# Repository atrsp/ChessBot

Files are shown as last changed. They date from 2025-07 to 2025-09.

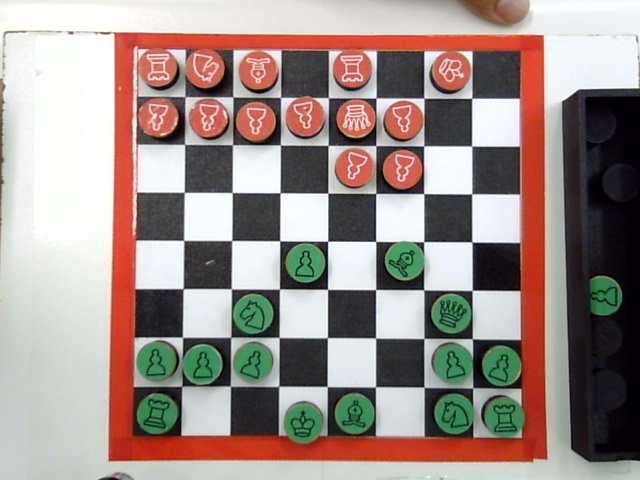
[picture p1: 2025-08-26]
server/vision/before.jpg

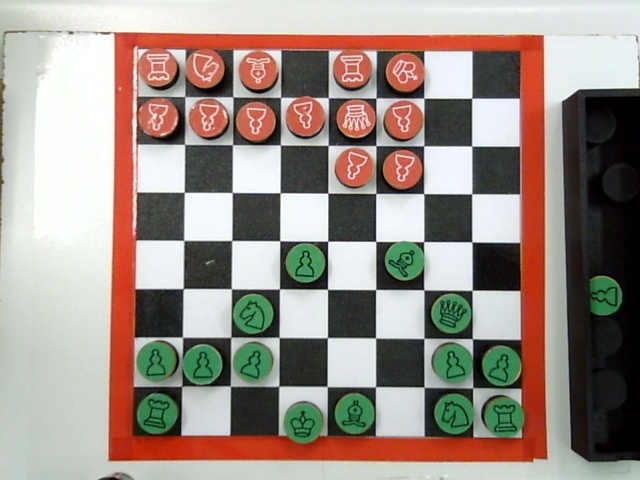
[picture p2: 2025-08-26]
server/vision/after.jpg

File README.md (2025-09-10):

# ChessBOT

## Visão Geral

O ChessBOT é um projeto de um jogador de xadrez autônomo, materializado em uma garra robótica capaz de disputar uma partida de xadrez contra um oponente humano de forma independente. O sistema utiliza visão computacional para identificar as jogadas do adversário, uma engine de xadrez para calcular seus próprios movimentos e um braço robótico para mover as peças no tabuleiro.

Este projeto foi desenvolvido como parte da disciplina [PROJETO INTEGRADO DE COMPUTAÇÃO II](https://computacao-ufes.github.io/mostra/pic2_EC_20251.html) na Universidade Federal do Espírito Santo (UFES).



### Autores
* [Ana Tereza Ribeiro Soares Pereira](https://github.com/atrsp)
* [Felipe Mattos Vanetti de Albuquerque](https://github.com/felipemattosv)
* [Luiz Felipe Machado](https://github.com/luizfelmach)
* [Vitor Dadalto Câmara Gomes](https://github.com/vitordcgomes)

---

## Componentes e Materiais

A seguir estão os itens utilizados na construção do ChessBOT.

### Componentes Eletrônicos e Estruturais
* **Microcontrolador:** ESP32
* **Servomotores:** 3 unidades do modelo Tower Pro MG995
* **Eletroímã:** 1 unidade com capacidade de 2kg
* **Webcam:** Logitech C720
* **Botões:** 2 Botões de Fliperama
* **Estrutura de Madeira:**
    * 1 Tábua de 45cm x 35cm
    * 1 "Ponte" de madeira com 55cm de altura

### Impressão 3D e Materiais Adicionais
* **Impressora 3D**
* **Filamento:** PLA
* **Peças:** 32 moedas de R$0,10
* **Acabamento:**
    * Papel Contact
    * Adesivos de papel para as peças

---

## Hardware e Impressão 3D

A estrutura física do braço robótico e suas peças foram produzidas com uma impressora 3D.

### Braço Robótico
O modelo base utilizado para o braço foi o [EEZYbotARM MK2](https://www.thingiverse.com/thing:1454048), um projeto gratuito desenvolvido por "daGHIZmo".

### Modificações e Melhorias
O modelo original serviu como ponto de partida, mas não possuía o alcance e a precisão necessários para a aplicação. Por isso, foi necessário remodelar algumas peças.

* **Engrenagem:** Após a montagem, foi identificada uma grande folga na engrenagem, causando uma imprecisão de uma casa no tabuleiro. A peça foi redesenhada para corrigir seu módulo, o que diminuiu a folga.
* **Base do Eletroímã:** O projeto original possuía uma garra na ponta do braço. Como o ChessBOT utiliza um eletroímã, foi modelada uma nova peça para acoplar este componente.

### Peças de Xadrez
Foram desenvolvidas e impressas bases para as moedas para facilitar o movimento do braço ao pegar cada peça e aumentar a jogabilidade do oponente.

### Peças Auxiliares
Também foram impressos modelos 3D para componentes de suporte, como dois suportes para descarte de peças capturadas e dois suportes para os botões.

---

## Montagem

A montagem do braço robótico seguiu as instruções detalhadas no vídeo [EEZYbotARM MK2 3D Printed Robot Build - Chris's Basement](https://www.youtube.com/watch?v=R2MI-tpXyS4&ab_channel=ChrisRiley) de Chris Riley. Não foi feita nenhuma alteração nesse processo.

---

## Software

O software do ChessBOT é dividido em dois componentes principais: o sistema de visão computacional para detectar a jogada do oponente e a engine de xadrez para a tomada de decisão.

### Visão Computacional
Foi utilizada a biblioteca [**OpenCV**](https://opencv.org/) em Python para identificar a jogada do oponente. A estratégia consiste em capturar uma imagem do tabuleiro antes e outra depois do movimento do oponente para identificar as diferenças.

O processo ocorre em três etapas:

1.  **Identificação do Tabuleiro:** Uma máscara de cor vermelha é aplicada à imagem para destacar a borda do tabuleiro. Com isso, os pontos referentes às bordas são detectados para saber onde cortar a imagem.
2.  **Corte e Ajuste de Perspectiva:** A imagem passa por uma transformação de perspectiva (warp) para corrigir distorções causadas pelo ângulo da câmera, alinhando o tabuleiro em uma visão superior. Em seguida, a área é cortada, deixando apenas a região útil.
3.  **Detecção do Movimento:** Com as imagens "antes" e "depois" normalizadas, o sistema calcula a diferença entre elas. Uma operação com kernel é aplicada para reduzir ruídos. As diferenças mais significativas são usadas para determinar o movimento realizado.

### Engine de Xadrez
A inteligência do robô é fornecida pela [**Stockfish**](https://stockfishchess.org/), uma engine de xadrez de código aberto.

* **Funcionamento:** A Stockfish recebe a configuração atual do tabuleiro (a disposição das peças no tabuleiro) e calcula qual seria a melhor jogada.
* **Análise:** Além de sugerir a jogada, a engine fornece uma avaliação numérica que indica se as peças brancas ou pretas estão em vantagem e o tamanho dessa vantagem.

---

## Decisões de Projeto

Algumas decisões foram tomadas para garantir a funcionalidade e a robustez do sistema.

* **Botões de Confirmação:** Foram adicionados botões de confirmação de jogada para determinar o momento exato de tirar a foto que identificará o movimento do oponente.
* **Adesivos das Peças:** As cores vermelha e verde foram escolhidas por se diferenciarem bem do preto e branco do tabuleiro, facilitando a identificação da jogada por visão computacional.
---

## Organização do repositório

Neste repositório, além do código principal, que integra a visão computacional com a lógica de jogo e a engine de xadrez, também existe uma interface que facilita o mapeamento das posições do tabuleiro.

## Como rodar?

### Pré-requisitos

Antes de iniciar, garanta que você possui configurado em sua máquina:  
- Visual Studio Code ([VSCode](https://code.visualstudio.com/))
- Extensão [PlatformIO](https://platformio.org/install/ide?install=vscode) no VSCode  
- [Node.js v20.19.4](https://nodejs.org/en/download/)  
- [Python 3.13.5](https://www.python.org/downloads/)  
- [Mosquitto MQTT Broker](https://mosquitto.org/download/)  
- Webcam conectada ao computador  
- Sistema operacional Linux (ou adaptado para Windows/macOS, quando aplicável)
- O ESP32 e a máquina que estará responsável pelos servidores durante o jogo devem sempre estar conectados na mesma rede WiFi.
  - Para verificar o IP da sua máquina na rede, utilize `ifconfig`.

---

### Passo a Passo para rodar a interface de mapeamento (apenas durante a etapa de mapeamento das posições do tabuleiro).
     
1. Configure o **Mosquitto Broker**.  
   Edite o arquivo `/etc/mosquitto/mosquitto.conf` com o seguinte conteúdo:  
   ```conf
   listener 1883
   protocol mqtt

   listener 9001
   protocol websockets

   allow_anonymous true
   ```  
   Inicie o serviço:  
   ```bash
   sudo systemctl start mosquitto.service
   ```
   
2. Configuração do Hardware (ESP32):
   - Abra o **VSCode** com a extensão **PlatformIO**.  
   - Abra a pasta `Hardware/`.  
      - As dependências serão instaladas automaticamente via `platformio.ini`.
   - Configure as constantes no arquivo `Hardware/map.cpp` (nome e senha da rede Wi-Fi, IP do broker e tópico MQTT).
   - Compile e envie o código `map.cpp` para o ESP32 com o PlatformIO. Tenha em mente que somente o código que está dentro da pasta `src/` é compilado e enviado para o microcontrolador.

3. Acesse a interface de mapeamento:  
   - Entre na pasta `ui/`.  
   - Instale as dependências:  
     ```bash
     npm install
     ```  
   - Rode o servidor:  
     ```bash
     npm run dev
     ```  
   - Acesse em: [`http://localhost:3000`](http://localhost:3000).  

4. Salve os valores dos servos para cada posição do tabuleiro em `hardware/lib/board/board.hpp`
---

### Passo a Passo para rodar o Servidor de Inteligência (Engine + Visão Computacional).

1. Baixe o **Stockfish** em: [https://stockfishchess.org/download/](https://stockfishchess.org/download/).  
2. Mova o binário para:  
   ```bash
   /usr/local/bin/stockfish
   ```
   Ou altere a constante `STOCKFISH_PATH` no arquivo `server/src/main.py` com o caminho para o local da sua instalação da stockfish.

3. Vá para a pasta `server/` e crie um ambiente virtual:  
   ```bash
   python3 -m venv .venv
   source .venv/bin/activate
   ```  

4. Instale as dependências:  
   ```bash
   pip install -r requirements.txt
   ```  

5. Certifique-se de que a webcam está funcionando.  

6. Inicie o servidor Python:  
   ```bash
   python3 src/main.py
   ```  

---

### Configuração da Interface do Jogo
1. Configuração do Hardware (ESP32):
   - Abra o **VSCode** com a extensão **PlatformIO**.  
   - Abra a pasta `Hardware/`.  
      - As dependências serão instaladas automaticamente via `platformio.ini`.
   - Configure as constantes no arquivo `Hardware/main.cpp` (IP do servidor e porta do servidor criado na etapa anterior (Servidor de Inteligência)).
      - O nome e senha da rede WiFi também precisam ser alterados dentro da função `void setup()`
   - Compile e envie o código `main.cpp` para o ESP32 com o PlatformIO. Tenha em mente que somente o código que está dentro da pasta `src/` é compilado e enviado para o microcontrolador.
     
2. Entre na pasta `chess/`.  
3. Instale as dependências:  
   ```bash
   npm install
   ```  
4. Rode o servidor da interface:  
   ```bash
   npm run dev
   ```
5. Acesse o servidor em: [`http://localhost:3000`](http://localhost:3000).
6. Se precisar reiniciar o jogo, basta clicar no botão de reset no ESP32 e reorganizar as peças no tabuleiro.

---

## Fluxo Geral de Execução (Mapeamento das posições do tabuleiro):
1. Iniciar o **Broker MQTT (Mosquitto)** com o comando
   ```bash
   sudo systemctl start mosquitto.service
   ```
2. Alterar as constantes da rede WiFi e Broker no arquivo `hardware/map.cpp` e subir o código no **ESP32** pelo PlatformIO.  
3. Abrir a **Interface de Mapeamento** na pasta `ui/` com `npm run dev` em [`http://localhost:3000`](http://localhost:3000) para calibrar as posições do tabuleiro.
4. Salvar as posições mapeadas em `hardware/lib/board/board.hpp`.

## Fluxo Geral de Execução (Jogo completo):
1. Dentro da pasta `server/`, ative o **ambiente virtual (.venv)** rodando o seguinte comando.
   ```bash
   source .venv/bin/activate
   ```
2. Iniciar o **servidor Python** com Stockfish + visão computacional em `server/src/main.py`
3. Alterar as constantes da rede WiFi e IP do server python no arquivo `hardware/src/main.cpp` e subir o código no **ESP32** pelo PlatformIO.  
4. Abrir a **Interface do Jogo** na pasta `chess/` com `npm run dev` em [`http://localhost:3000`](http://localhost:3000) para começar a jogar contra o braço robótico.  

### Opcional:
A parte de visão computacional (identificação de movimentação das peças) pode ser testada separadamente via Jupyter Notebook na pasta `server/vision/`:

   - O arquivo `takepic.py` é útil para descomplicar o processo de tirar uma foto antes e depois de mudar uma peça de uma posição para outra no tabuleiro e pode ser rodado primeiro para armazenar as fotos `before.jpg` e `after.jpg`   
   - O Notebook `main.ipynb` carrega as imagens `before.jpg` e `after.jpg` e mostra todo o processamento sobre as imagens para identificar em quais posições do tabuleiro houve mudança. É útil para debuggar possíveis erros de identificação da jogada do oponente que possam ocorrer durante o jogo.

***
***

# ChessBOT (English)

## Overview

ChessBOT is an autonomous chess player project, embodied by a robotic arm capable of playing a game of chess against a human opponent on its own. The system uses computer vision to identify the opponent's moves, a chess engine to calculate its own moves, and a robotic arm to move the pieces on the board.

This project was developed as part of the "INTEGRATED COMPUTING PROJECT II" course at the Federal University of Espírito Santo.

### Authors
* [Ana Tereza Ribeiro Soares Pereira](https://github.com/atrsp)
* [Felipe Mattos Vanetti de Albuquerque](https://github.com/felipemattosv)
* [Luiz Felipe Machado](https://github.com/luizfelmach)
* [Vitor Dadalto Câmara Gomes](https://github.com/vitordcgomes)

---

## Components and Materials

The following are the items used in the construction of the ChessBOT.

### Electronic and Structural Components
* **Microcontroller:** ESP32
* **Servo Motors:** 3 units of the Tower Pro MG995 model
* **Electromagnet:** 1 unit with a 2kg capacity
* **Webcam:** Logitech C720
* **Buttons:** 2 Arcade Buttons
* **Wooden Structure:**
    * 1 45cm x 35cm wooden board
    * 1 wooden "bridge" with a height of 55cm

### 3D Printing and Additional Materials
* **3D Printer**
* **Filament:** PLA
* **Pieces:** 32 Brazilian 10-cent coins
* **Finishing:**
    * Contact Paper
    * Paper stickers for the pieces

---

## Hardware and 3D Printing

The physical structure of the robotic arm and its parts were produced using a 3D printer.

### Robotic Arm
The base model used for the arm was the [EEZYbotARM MK2](https://www.thingiverse.com/thing:1454048), a free design developed by "daGHIZmo".

### Modificações and Improvements
The original model served as a starting point, but it lacked the necessary reach and precision for the application. Therefore, it was necessary to remodel some parts.

* **Gear:** After assembly, a large backlash was identified in the gear, causing an imprecision of one square on the board. The part was redesigned to correct its module, which reduced the backlash.
* **Electromagnet Base:** The original design featured a claw at the end of the arm. As the ChessBOT uses an electromagnet, a new part was modeled to attach this component.

###Chess Pieces
Bases for the coins were developed and printed to make it easier for the arm to pick up each piece and to improve the opponent's gameplay experience.

### Auxiliary Parts
3D models were also printed for support components, such as two holders for captured pieces and two holders for the buttons.

---

## Assembly

The assembly of the robotic arm followed the detailed instructions in the video [EEZYbotARM MK2 3D Printed Robot Build - Chris's Basement](https://www.youtube.com/watch?v=R2MI-tpXyS4&ab_channel=ChrisRiley) by Chris Riley. No alterations were made to this process.

---

## Software

The ChessBOT's software is divided into two main components: the computer vision system to detect the opponent's move and the chess engine for decision-making.

### Computer Vision
The [**OpenCV**](https://opencv.org/) library in Python was used to identify the opponent's move. The strategy is to capture an image of the board before and another after the opponent's move to identify the differences.

The process occurs in three stages:

1.  **Board Identification:** A red color mask is applied to the image to highlight the board's border. This allows the detection of the points corresponding to the borders to know where to crop the image.
2.  **Cropping and Perspective Adjustment:** The image undergoes a perspective transformation (warp) to correct distortions caused by the camera angle, aligning the board to a top-down view. Then, the area is cropped, leaving only the useful region.
3.  **Move Detection:** With the normalized "before" and "after" images, the system calculates the difference between them. A kernel operation is applied to reduce noise. The most significant differences are used to determine the move that was made.

### Chess Engine
The robot's intelligence is provided by [**Stockfish**](https://stockfishchess.org/), an open-source chess engine.

* **Functionality:** Stockfish receives the current board configuration (the "position") and calculates what the best move would be.
* **Analysis:** In addition to suggesting a move, the engine provides a numerical evaluation that indicates whether the white or black pieces have an advantage and the size of that advantage.

---

## Design Decisions

Certain decisions were made to ensure the system's functionality and robustness.

* **Confirmation Buttons:** Move confirmation buttons were added to determine the exact moment to take the photo that will identify the opponent's move.
* **Piece Stickers:** The red and green colors were chosen because they differentiate well from the black and white of the board, facilitating the move identification by computer vision.

## How to run?

### Prerequisites

Before you start, make sure your machine has:

* Visual Studio Code ([VSCode](https://code.visualstudio.com/))
* [PlatformIO extension](https://platformio.org/install/ide?install=vscode) in VSCode
* [Node.js v20.19.4](https://nodejs.org/en/download/)
* [Python 3.13.5](https://www.python.org/downloads/)
* [Mosquitto MQTT Broker](https://mosquitto.org/download/)
* A webcam connected to the computer
* Linux operating system (or adapted for Windows/macOS where applicable)
* The ESP32 and the machine responsible for running the servers during the game must always be connected to the same Wi-Fi network.

  * To check your machine’s IP on the network, use `ifconfig`.

---

### Step-by-step to run the mapping interface (only during the board-position mapping stage).

1. Configure the **Mosquitto Broker**.
   Edit `/etc/mosquitto/mosquitto.conf` with the following content:

   ```conf
   listener 1883
   protocol mqtt

   listener 9001
   protocol websockets

   allow_anonymous true
   ```

   Start the service:

   ```bash
   sudo systemctl start mosquitto.service
   ```

2. Hardware Setup (ESP32):

   * Open **VSCode** with the **PlatformIO** extension.
   * Open the `Hardware/` folder.

     * Dependencies will be installed automatically via `platformio.ini`.
   * Set the constants in `Hardware/map.cpp` (Wi-Fi SSID and password, broker IP, and MQTT topic).
   * Compile and upload `map.cpp` to the ESP32 with PlatformIO. Keep in mind that only the code inside the `src/` folder is compiled and uploaded to the microcontroller.

3. Access the mapping interface:

   * Go into the `ui/` folder.
   * Install dependencies:

     ```bash
     npm install
     ```
   * Run the dev server:

     ```bash
     npm run dev
     ```
   * Open: [`http://localhost:3000`](http://localhost:3000).

4. Save the servo values for each board position in `hardware/lib/board/board.hpp`

---

### Step-by-step to run the Intelligence Server (Engine + Computer Vision).

1. Download **Stockfish** at: [https://stockfishchess.org/download/](https://stockfishchess.org/download/).

2. Move the binary to:

   ```bash
   /usr/local/bin/stockfish
   ```

   Or change the `STOCKFISH_PATH` constant in `server/src/main.py` to the path where Stockfish is installed on your system.

3. Go to the `server/` folder and create a virtual environment:

   ```bash
   python3 -m venv .venv
   source .venv/bin/activate
   ```

4. Install dependencies:

   ```bash
   pip install -r requirements.txt
   ```

5. Make sure the webcam is working.

6. Start the Python server:

   ```bash
   python3 src/main.py
   ```

---

### Game Interface Setup

1. Hardware Setup (ESP32):

   * Open **VSCode** with the **PlatformIO** extension.
   * Open the `Hardware/` folder.

     * Dependencies will be installed automatically via `platformio.ini`.
   * Set the constants in `Hardware/main.cpp` (server IP and the port of the server created in the previous step—Intelligence Server).

     * The Wi-Fi SSID and password also need to be set inside the `void setup()` function.
   * Compile and upload `main.cpp` to the ESP32 with PlatformIO. Keep in mind that only the code inside the `src/` folder is compiled and uploaded to the microcontroller.
2. Go into the `chess/` folder.
3. Install dependencies:

   ```bash
   npm install
   ```
4. Run the interface server:

   ```bash
   npm run dev
   ```
5. Access the interface at: [`http://localhost:3000`](http://localhost:3000).
6. If you need to restart the game, just press the reset button on the ESP32 and rearrange the pieces on the board.

---

## Overall Execution Flow (Board position mapping):

1. Start the **MQTT Broker (Mosquitto)** with:

   ```bash
   sudo systemctl start mosquitto.service
   ```
2. Update the Wi-Fi and Broker constants in `hardware/map.cpp` and upload the code to the **ESP32** via PlatformIO.
3. Open the **Mapping Interface** in the `ui/` folder with `npm run dev` at [`http://localhost:3000`](http://localhost:3000) to calibrate the board positions.
4. Save the mapped positions in `hardware/lib/board/board.hpp`.

## Overall Execution Flow (Full game):

1. Inside the `server/` folder, activate the **virtual environment (.venv)** by running:

   ```bash
   source .venv/bin/activate
   ```
2. Start the **Python server** with Stockfish + computer vision at `server/src/main.py`.
3. Update the Wi-Fi constants and the Python server IP in `hardware/src/main.cpp` and upload the code to the **ESP32** via PlatformIO.
4. Open the **Game Interface** in the `chess/` folder with `npm run dev` at [`http://localhost:3000`](http://localhost:3000) to start playing against the robotic arm.

### Optional:

The computer vision component (identifying piece movement) can be tested separately via Jupyter Notebook in the `server/vision/` folder:

* The `takepic.py` file is useful to simplify taking a photo before and after moving a piece from one square to another, and can be run first to store the `before.jpg` and `after.jpg` images.
* The `main.ipynb` notebook loads `before.jpg` and `after.jpg` and shows the entire processing pipeline on the images to identify which board squares changed. It’s useful for debugging possible errors in detecting the opponent’s move that may occur during the game.

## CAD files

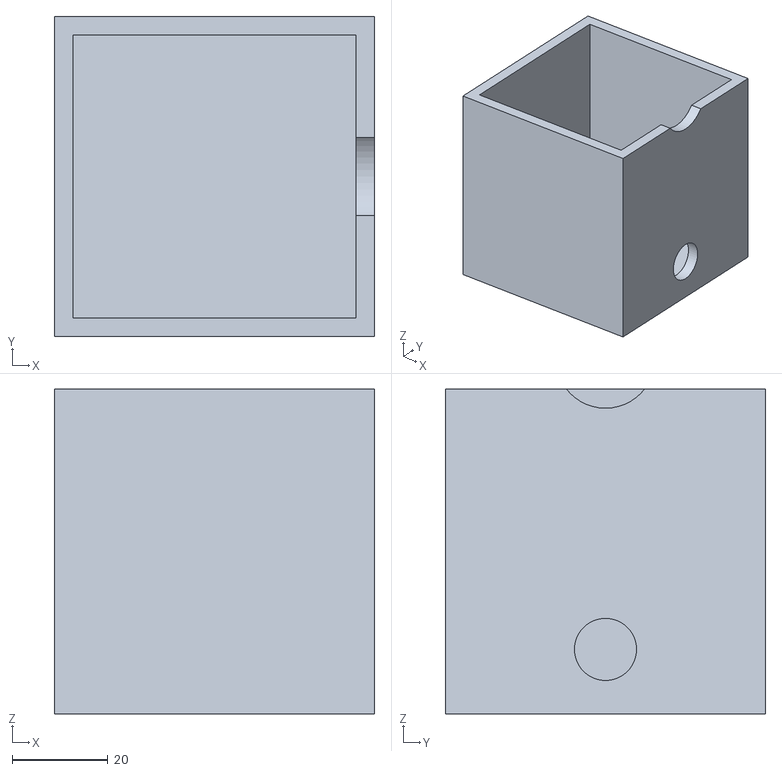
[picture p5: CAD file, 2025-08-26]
3D/buttonBox/corpo_caixa (1).stl
67.0 x 67.0 x 68.0

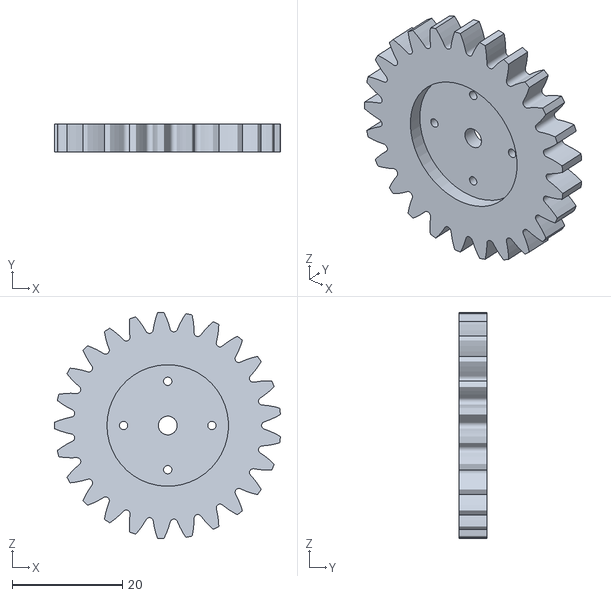
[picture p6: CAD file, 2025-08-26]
3D/EEZYbotARMMk2_changes/Engrenagem_pequena_nova.stl
40.9 x 5.00 x 41.0

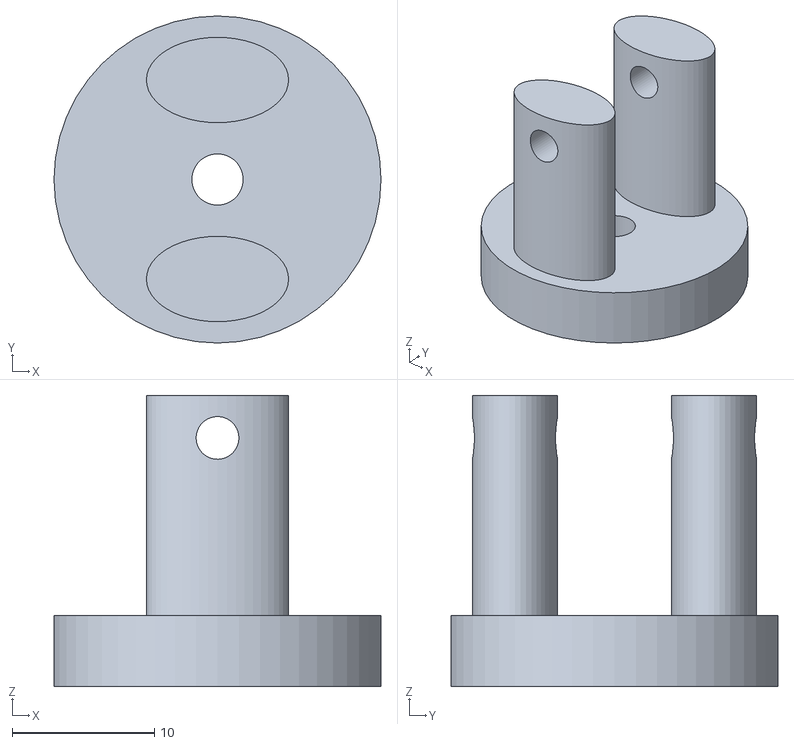
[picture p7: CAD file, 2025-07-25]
3D/electromagnetBase/encaixe_eletroima.stl
23.0 x 23.0 x 20.5

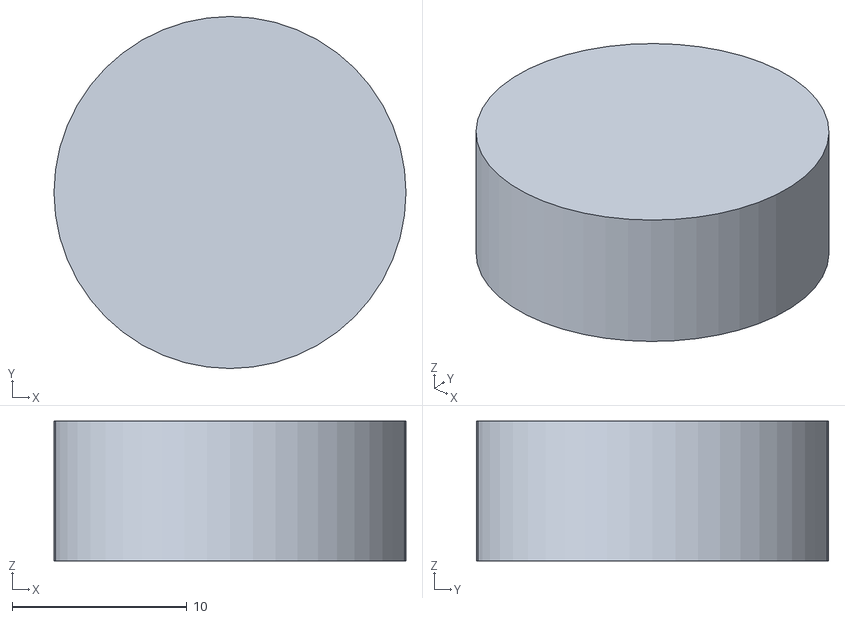
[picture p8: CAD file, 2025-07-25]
3D/pieceBase/semParede.stl
20.1 x 20.2 x 8.00

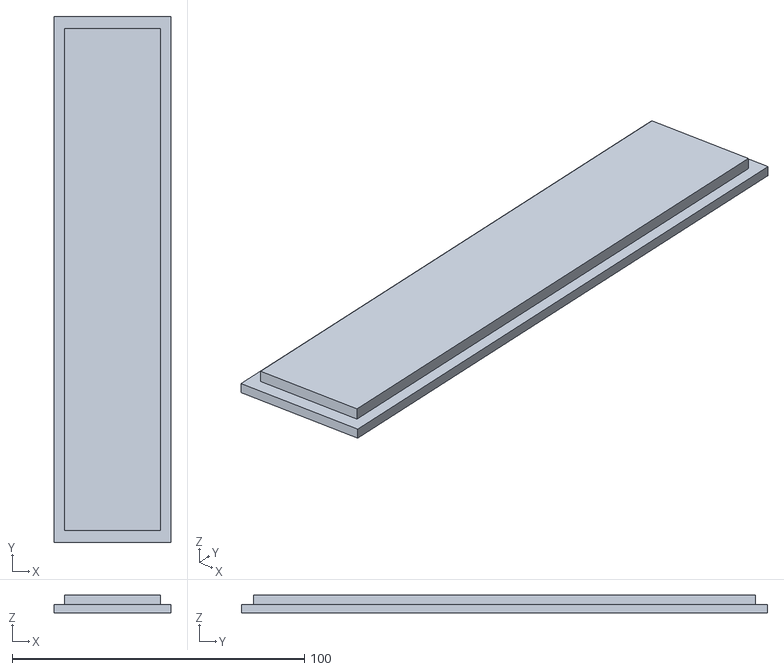
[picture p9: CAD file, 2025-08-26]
3D/pieceTrash/tampa_lixo (1).stl
40.0 x 180.0 x 6.00

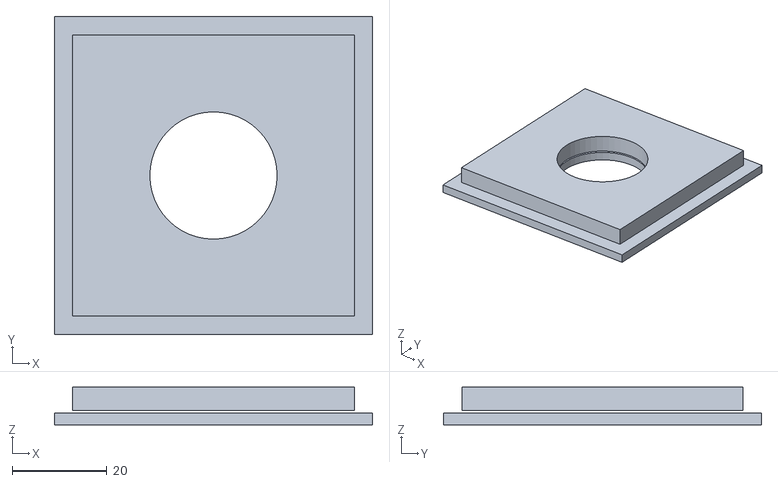
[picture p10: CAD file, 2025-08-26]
3D/buttonBox/tampa_caixa (1).stl
67.0 x 67.0 x 8.00

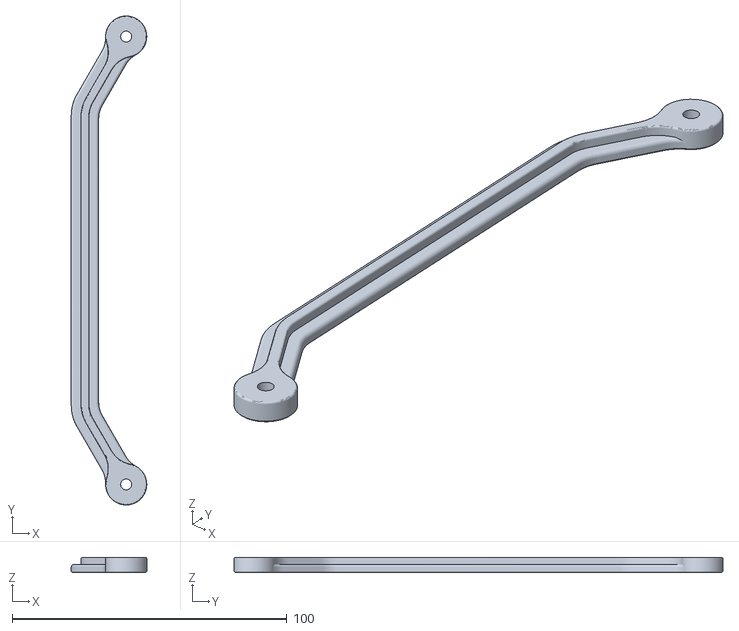
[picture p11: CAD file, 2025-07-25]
3D/EEZYbotARMMk2_changes/increasedArm.stl
27.5 x 178.0 x 5.50

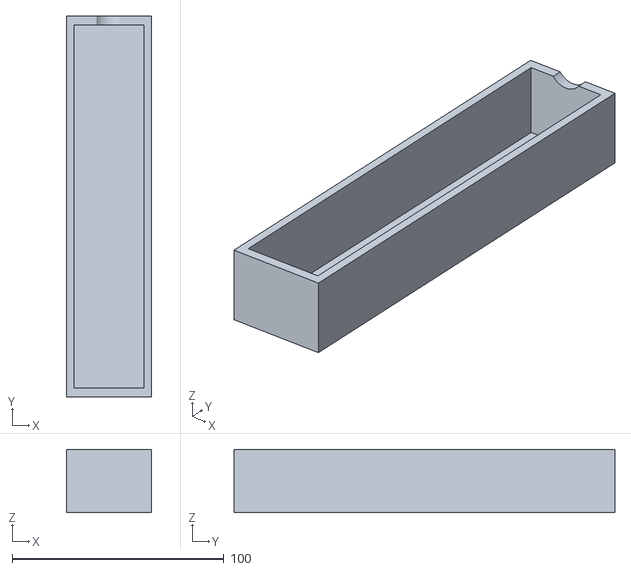
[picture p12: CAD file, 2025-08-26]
3D/pieceTrash/corpo_lixo (1).stl
40.0 x 180.0 x 30.0

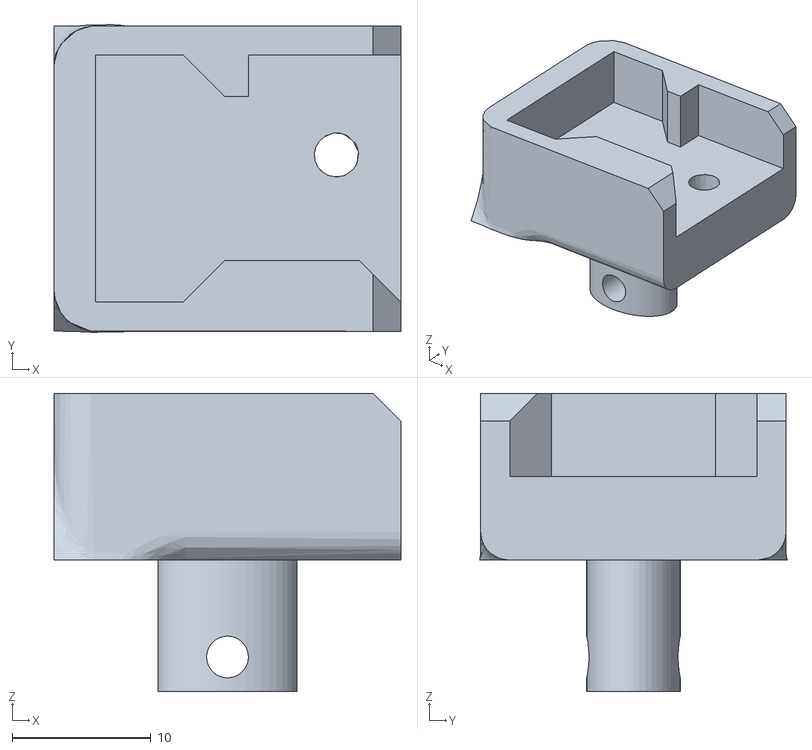
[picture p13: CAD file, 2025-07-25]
3D/EEZYbotARMMk2_changes/electromagnetFit.stl
25.0 x 22.2 x 21.5

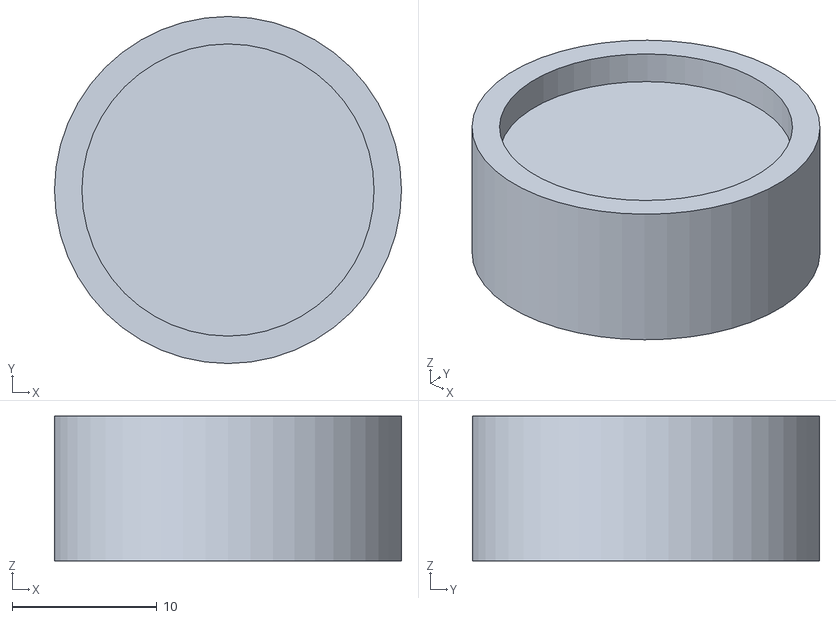
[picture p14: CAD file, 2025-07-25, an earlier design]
3D/unusedPieces/paredeGrossa.stl
24.0 x 24.0 x 10.0

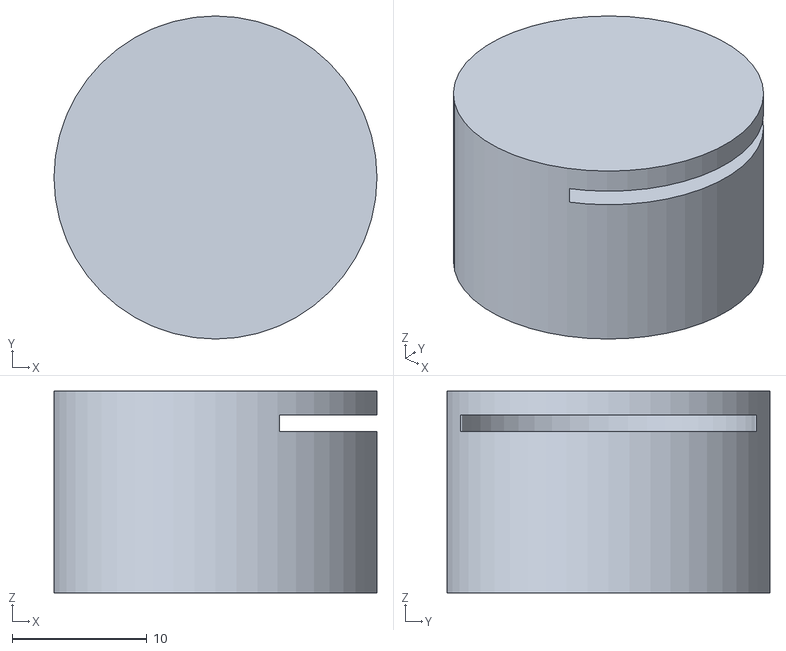
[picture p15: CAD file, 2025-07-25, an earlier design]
3D/unusedPieces/tetoGrosso.stl
24.0 x 24.0 x 15.0

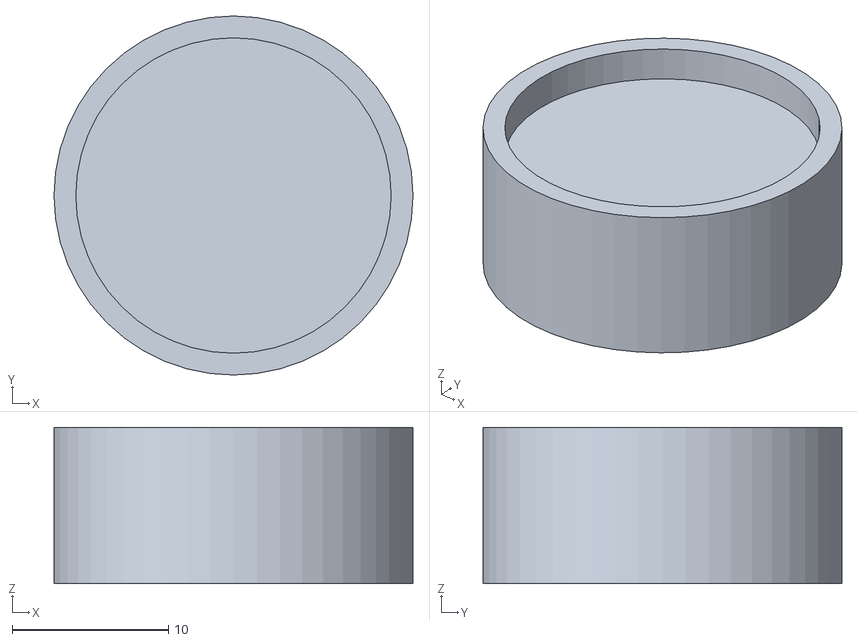
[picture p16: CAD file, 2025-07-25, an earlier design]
3D/unusedPieces/paredeFina.stl
23.0 x 23.0 x 10.0

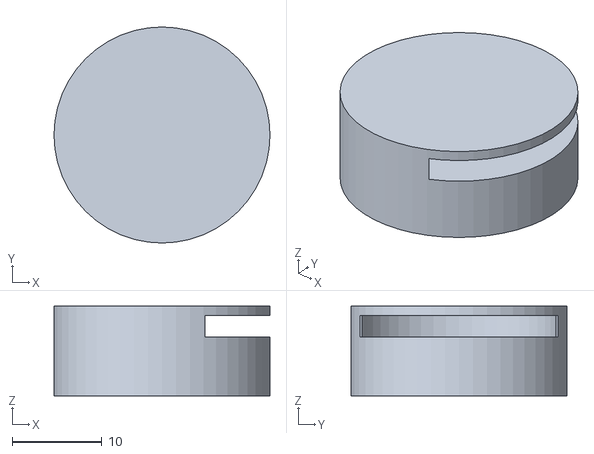
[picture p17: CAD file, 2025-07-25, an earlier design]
3D/unusedPieces/moeda_shodebola.stl
24.0 x 24.0 x 10.00

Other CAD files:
3D/unusedPieces/tetoFino.stl

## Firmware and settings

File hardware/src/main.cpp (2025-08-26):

#include <ArduinoJson.h>
#include <Bounce2.h>
#include <HTTPClient.h>

#include <board.hpp>
#include <servo.hpp>
#include <utils.hpp>

#define pinServoBase 18
#define pinServoLeft 19
#define pinServoRight 21
#define pinConfirm 25
#define pinMagnet 32

ServoChess  servoBase(pinServoBase, POS_INITIAL.base);
ServoChess  servoLeft(pinServoLeft, POS_INITIAL.left);
ServoChess  servoRight(pinServoRight, POS_INITIAL.right);
HTTPClient  http;
const char* server  = "http://172.20.10.8:5000";
Bounce      confirm = Bounce();

class Move {
   public:
    int row;
    int column;

    Move() {
    }

    Move(int row, int column) {
        this->row    = row;
        this->column = column;
    }
};

class BestMove {
   public:
    Move from;
    Move to;
    bool captured;
    int  castling;

    BestMove() {
    }

    BestMove(Move from, Move to, bool captured, int castling) {
        this->from     = from;
        this->to       = to;
        this->captured = captured;
        this->castling = castling;
    }
};

void gotoPositionDown(ServoPosition p, VerticalTuning f) {
    servoBase.move(p.base);

    servoRight.move(p.right, f.percent);
    servoLeft.move(p.left, f.percent);

    int remainingLeft  = abs(servoLeft.position - p.left);
    int remainingRight = abs(servoRight.position - p.right);

    int stepsRight = remainingRight / f.deltaRight;
    int stepsLeft  = remainingLeft / f.deltaLeft;

    while (stepsRight > 0 and stepsLeft > 0) {
        if (stepsLeft > 0 and servoLeft.position != p.left) {
            servoLeft.moveStep(p.left, f.deltaLeft);
            stepsLeft--;
        }
        if (stepsRight > 0 and servoRight.position != p.right) {
            servoRight.moveStep(p.right, f.deltaRight);
            stepsRight--;
        }
    }

    servoRight.move(p.right);
    servoLeft.move(p.left);
}

void gotoPositionUp(ServoPosition p, VerticalTuning f) {
    float percent        = 1 - f.percent;
    int   remainingLeft  = abs((servoLeft.position - p.left) * percent);
    int   remainingRight = abs((servoRight.position - p.right) * percent);

    int stepsRight = remainingRight / f.deltaRight;
    int stepsLeft  = remainingLeft / f.deltaLeft;

    while (stepsRight > 0 and stepsLeft > 0) {
        if (stepsRight > 0 and servoRight.position != p.right) {
            servoRight.moveStep(p.right, f.deltaRight);
            stepsRight--;
        }
        if (stepsLeft > 0 and servoLeft.position != p.left) {
            servoLeft.moveStep(p.left, f.deltaLeft);
            stepsLeft--;
        }
    }

    servoRight.move(p.right);
    servoLeft.move(p.left);

    servoBase.move(p.base);
}

void gotoPositionCamera() {
    servoBase.move(POS_CAMERA.base);
    servoRight.move(POS_CAMERA.right);
    servoLeft.move(POS_CAMERA.left);
}

void gotoPositionDefault() {
    servoLeft.pos_default();
    servoRight.pos_default();
    servoBase.pos_default();
}

void waitKey() {
    while (1) {
        confirm.update();
        if (confirm.fell()) {
            break;
        }
    }
}

void disableMagnet() {
    digitalWrite(pinMagnet, LOW);
}

void enableMagnet() {
    digitalWrite(pinMagnet, HIGH);
}

void captureBoardState() {
    gotoPositionCamera();
    delay(500);
    String url = String(server) + String("/capture-board-state");
    http.begin(url);
    int httpCode = http.GET();
    http.end();
}

BestMove getBestMove() {
    String url = String(server) + String("/get-best-move");
    http.begin(url);
    int httpCode = http.GET();

    Serial.println(httpCode);
    Serial.printf("HTTP CODE DO BEST MOVE: %d\n", httpCode);

    if (httpCode == 200) {
        String payload = http.getString();
        Serial.println(payload);
        StaticJsonDocument<256> doc;
        DeserializationError    error = deserializeJson(doc, payload);

        if (!error) {
            int  from_row = doc["from"][0];
            int  from_col = doc["from"][1];
            int  to_row   = doc["to"][0];
            int  to_col   = doc["to"][1];
            bool captured = doc["captured"];
            int  castling = doc["castling"];
            Move from(from_row, from_col);
            Move to(to_row, to_col);

            Serial.printf("From: (%d, %d)\n", from_row, from_col);
            Serial.printf("To: (%d, %d)\n", to_row, to_col);
            Serial.printf("Captured: %d Castling: %d\n", captured, castling);

            return BestMove(from, to, captured, castling);
        }
    }

    http.end();

    Serial.println("Deu merdaaa!!!!!!!!!!!!!!!");

    while (Serial.available() == 0) delay(100);
    Serial.read();

    return BestMove();
}

void executeRobotMove(BestMove move) {
    Serial.println("Executando jogada no ROBO...");

    gotoPositionDefault();

    ServoPosition  from = CHESSBOARD_POSITIONS[move.from.row][move.from.column];
    VerticalTuning from_vt =
        CHESSBOARD_VERTICAL_TUNNING[move.from.row][move.from.column];

    ServoPosition  to = CHESSBOARD_POSITIONS[move.to.row][move.to.column];
    VerticalTuning to_vt =
        CHESSBOARD_VERTICAL_TUNNING[move.to.row][move.to.column];

    if (move.captured) {
        gotoPositionDown(to, to_vt);
        delay(500);
        enableMagnet();
        gotoPositionUp(POS_THRASH, to_vt);
        delay(500);
        disableMagnet();
        gotoPositionDefault();
    }

    gotoPositionDown(from, from_vt);
    delay(1000);
    enableMagnet();
    delay(500);
    gotoPositionUp(POS_INITIAL, from_vt);

    delay(1000);
    gotoPositionDown(to, to_vt);
    delay(500);
    disableMagnet();
    gotoPositionUp(POS_INITIAL, to_vt);

    if (move.castling) {
        gotoPositionDefault();
        if (move.castling == 1) {
            ServoPosition  from    = CHESSBOARD_POSITIONS[7][0];
            VerticalTuning from_vt = CHESSBOARD_VERTICAL_TUNNING[7][0];

            ServoPosition  to    = CHESSBOARD_POSITIONS[7][2];
            VerticalTuning to_vt = CHESSBOARD_VERTICAL_TUNNING[7][2];

            gotoPositionDown(from, from_vt);
            delay(1000);
            enableMagnet();
            delay(500);
            gotoPositionUp(POS_INITIAL, from_vt);

            delay(1000);
            gotoPositionDown(to, to_vt);
            delay(500);
            disableMagnet();
            gotoPositionUp(POS_INITIAL, to_vt);
        }

        if (move.castling == 2) {
            ServoPosition  from    = CHESSBOARD_POSITIONS[7][7];
            VerticalTuning from_vt = CHESSBOARD_VERTICAL_TUNNING[7][7];

            ServoPosition  to    = CHESSBOARD_POSITIONS[7][4];
            VerticalTuning to_vt = CHESSBOARD_VERTICAL_TUNNING[7][4];

            gotoPositionDown(from, from_vt);
            delay(1000);
            enableMagnet();
            delay(500);
            gotoPositionUp(POS_INITIAL, from_vt);

            delay(1000);
            gotoPositionDown(to, to_vt);
            delay(500);
            disableMagnet();
            gotoPositionUp(POS_INITIAL, to_vt);
        }
    }
}

void waitOpponentMove() {
    Serial.println("15 segundos para fazer a jogada");
    waitKey();
}

void confirmRobotMove() {
    Serial.println("15 segundos para CONFIRMAR a jogada");
    waitKey();
}

void resetGame() {
    String url = String(server) + String("/reset");
    http.begin(url);
    int httpCode = http.GET();
    http.end();
}

void setup() {
    Serial.begin(115200);

    setup_wifi("iPhone de Felipe", "felipeoi");

    pinMode(pinMagnet, OUTPUT);
    digitalWrite(pinMagnet, LOW);

    pinMode(pinConfirm, INPUT_PULLUP);
    confirm.attach(pinConfirm);
    confirm.interval(50);
    gotoPositionDefault();

    resetGame();
}

void loop() {
    // enableMagnet();
    // delay(5000);
    //
    // for (int j = 0; j < 8; j++) {
    //    ServoPosition  p = CHESSBOARD_POSITIONS[6][j];
    //    VerticalTuning f = CHESSBOARD_VERTICAL_TUNNING[6][j];
    //    gotoPositionDown(p, f);
    //    disableMagnet();
    //    delay(1000);
    //    enableMagnet();
    //
    //    gotoPositionUp(POS_INITIAL, f);
    //    delay(2000);
    //}
    //
    // disableMagnet();
    // while (1);

    captureBoardState();
    waitOpponentMove();

    int httpCode = -1;

    while (httpCode < 0) {
        String url = String(server) + String("/confirm-opponent-move");

        http.begin(url);
        httpCode = http.GET();
        http.end();
        Serial.printf("HTT CODE: %d\n", httpCode);
    }

    BestMove move = getBestMove();
    executeRobotMove(move);
    confirmRobotMove();
}

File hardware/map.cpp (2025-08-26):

#include <WiFi.h>
#include <PubSubClient.h>
#include <ESP32Servo.h>
#include <math.h>

// Wi-Fi
const char* ssid = "iPhone de Felipe";
const char* password = "felipeoi";


// MQTT
const char* mqtt_server = "172.20.10.8";
const char* mqtt_topic = "braco/comando";

WiFiClient espClient;
PubSubClient client(espClient);

// Pinos
#define pinServBase     18
#define pinServEsquerda 19
#define pinServDireita  21
#define pinMagnet       32

// Servos
Servo servBase, servEsquerda, servDireita;

// Posições atuais em microssegundos
int posBase     = 2500;
int posEsquerda = 2500;
int posDireita  = 1100;

// Função de easing
float easeInOut(float t) {
  return 0.5 * (1 - cos(t * PI));
}

// Movimento suave com easing
void moverServoSuave(Servo& servo, int& atual, int destino, int duracaoMs = 1000, int passos = 50) {
  int delta = abs(destino - atual);

  if (delta <= 222) {  // ~30°
    int passo = (destino > atual) ? 1 : -1;
    int delayPorUs = duracaoMs * 1000L / max(delta, 1);
    for (int us = atual; us != destino; us += passo) {
      servo.writeMicroseconds(us);
      delayMicroseconds(delayPorUs);
    }
    servo.writeMicroseconds(destino);
  } else {
    for (int i = 0; i <= passos; i++) {
      float t = (float)i / passos;
      float curva = easeInOut(t);
      int valorInterpolado = atual + (destino - atual) * curva;
      servo.writeMicroseconds(valorInterpolado);
      delayMicroseconds((duracaoMs * 1000L) / passos);
    }
  }

  atual = destino;
}

void setup_wifi() {
  WiFi.mode(WIFI_STA);
  WiFi.begin(ssid, password);
  while (WiFi.status() != WL_CONNECTED) {
    delay(500);
    Serial.print(".");
  }
  Serial.println("\nWiFi conectado");
}

void callback(char* topic, byte* payload, unsigned int length) {
  String msg;
  for (int i = 0; i < length; i++) {
    msg += (char)payload[i];
  }
  msg.trim();
  Serial.print("Comando recebido: ");
  Serial.println(msg);

  // Esperado: base|esquerdo|direito|magnet
  int sep1 = msg.indexOf('|');
  int sep2 = msg.indexOf('|', sep1 + 1);
  int sep3 = msg.indexOf('|', sep2 + 1);

  if (sep1 == -1 || sep2 == -1 || sep3 == -1) {
    Serial.println("Formato inválido!");
    return;
  }

  int base     = msg.substring(0, sep1).toInt();
  int esquerdo = msg.substring(sep1 + 1, sep2).toInt();
  int direito  = msg.substring(sep2 + 1, sep3).toInt();
  int magnet   = msg.substring(sep3 + 1).toInt();

  Serial.printf("----> %dus %dus %dus magnet=%d\n", base, esquerdo, direito, magnet);

  moverServoSuave(servBase, posBase, base);
  moverServoSuave(servEsquerda, posEsquerda, esquerdo);
  moverServoSuave(servDireita, posDireita, direito);

  digitalWrite(pinMagnet, magnet == 1 ? HIGH : LOW);
}

void reconnect() {
  while (!client.connected()) {
    if (client.connect("ESP32Client")) {
      client.subscribe(mqtt_topic);
      Serial.println("MQTT conectado!");
    } else {
      Serial.print("Falha MQTT, rc=");
      Serial.print(client.state());
      Serial.println(" tentando novamente em 5s...");
      delay(5000);
    }
  }
}

void posDefault() {
  moverServoSuave(servBase, posBase, 2500);
  delay(100);
  moverServoSuave(servEsquerda, posEsquerda, 2680);
  delay(100);
  moverServoSuave(servDireita, posDireita, 1100);
  delay(100);
}

void setup() {
  Serial.begin(115200);

  servBase.attach(pinServBase);
  servEsquerda.attach(pinServEsquerda);
  servDireita.attach(pinServDireita);
  pinMode(pinMagnet, OUTPUT);
  digitalWrite(pinMagnet, LOW);

  setup_wifi();
  client.setServer(mqtt_server, 1883);
  client.setCallback(callback);

  posDefault();
}

void loop() {
  if (!client.connected()) {
    reconnect();
  }
  client.loop();
}

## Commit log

2025-07-24 add 3D files
    [braco aumentado.stl, buraco_certo.stl, encaixe_braco.stl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]
2025-07-24 New stl files
    [paredeFina.stl, paredeGrossa.stl, semParede.stl]
2025-08-26 Organizing 3D files
    [Engrenagem_pequena_nova.stl, corpo_caixa (1).stl, corpo_lixo (1).stl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]
